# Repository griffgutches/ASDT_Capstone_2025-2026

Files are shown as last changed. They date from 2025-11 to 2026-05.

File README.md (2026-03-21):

# ASDT Datalogger
This PCB is a rocketry flight datalogger with a comprehensive sensor suite.

## Features
- GPS
- Radio
- IMU
- Barometer
- Magnetometer
- Status LEDs
- Reverse polarity protection

## Parts
- ESP32-S3 microcontroller
- u-blox MAX-M10S GPS
- RFM95W-915 radio (SX1276)
- ISM6HG256X High/Low-G IMU
- BMI088 Low-G IMU
- ADXL375 High-G IMU
- MS5607 barometer
- BMP390 barometer
- MMC5983MA magnetometer

## Pinout
| GPIO | Function |
|---|---|
| 0 | BOOT |
| 1 | MS5607 Baro CS |
| 2 | BMP390 Baro CS |
| 4 | MMC598 Mag CS |
| 7 | Radio CS |
| 14 | BMI088 Gyro CS |
| 21 | ADXL375 IMU CS |
| 40 | BMI088 Accel CS |
| 41 | ISM6HG256X IMU CS |
| 11 | ADXL375 INT |
| 13 | Radio INT |
| 18 | BMI088 Accel INT |
| 31 | GPS INT |
| 42 | MMC598 Mag INT |
| 10 | MISO |
| 17 | SCK |
| 44 | MOSI |
| 45 | SCL* |
| 46 | SDA* |
| 25 | Flash I03 |
| 26 | Flash I02 |
| 27 | Flash CS |
| 28 | Flash CLK |
| 29 | Flash IO1 |
| 30 | Flash IO0 |
| 35 | SD CMD |
| 37 | SD data 0 |
| 38 | SD data 1 |
| 33 | SD data 2 |
| 34 | SD data 3 |
| 36 | SD clock |
| 15 | XTAL_32K_P |
| 16 | XTAL_32K_N |
| 19 | USB_D- |
| 20 | USB_D+ |
| 8 | Timepulse |
| 9 | Battery Sense |
| 39 | Buzzer |
| 43 | ANT_SW |
| 6 | Radio Busy |

*SDA/SCL should be moved off GPIO45/46 on future designs because they are strapping pins

## Addresses
| Name | Part | I2C Address |
|---|---|---|
| GPS | MAX-M10S | 0x42 **** |

## Notes
- The boot and reset button on the board are enabled by the jumper J5 on the left side of the board, this jumper must be removed before flight
- The radio **may be damaged** if it is run without an antenna attached
- The LED data pin should never be floating
- The battery sense pin is connected through a 300k-100k voltage divider, so the pin voltage is 0.25 times the battery voltage
- The total current consumption should be below 500mA continuous
- The GPS will blink an LED near the bottom of the board once per second once it gets a fix

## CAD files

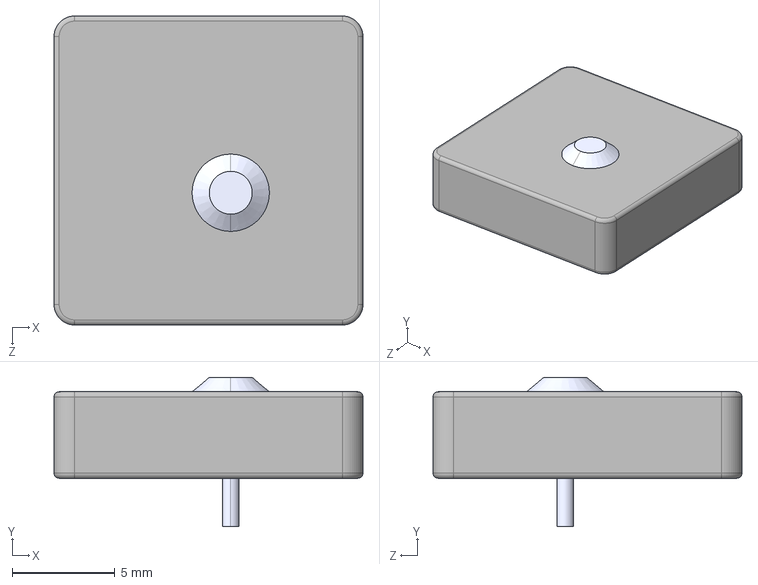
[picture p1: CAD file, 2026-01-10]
Data_Logger_KiCAD/3DModels/YG0043AA.STEP
15.0 x 7.25 x 15.0 mm

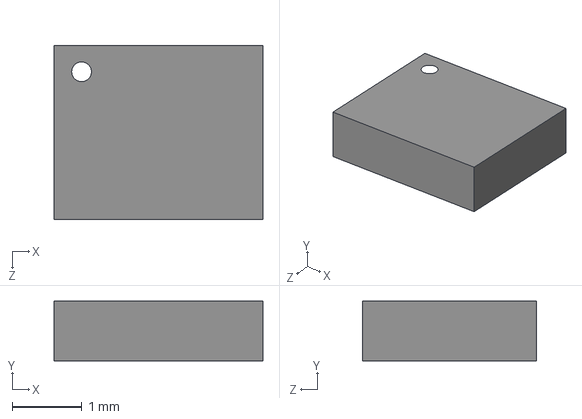
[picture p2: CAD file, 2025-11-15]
Symbol_Files/LSM6DSO32TR/LSM6DSO32TR.step
3.00 x 0.86 x 2.50 mm

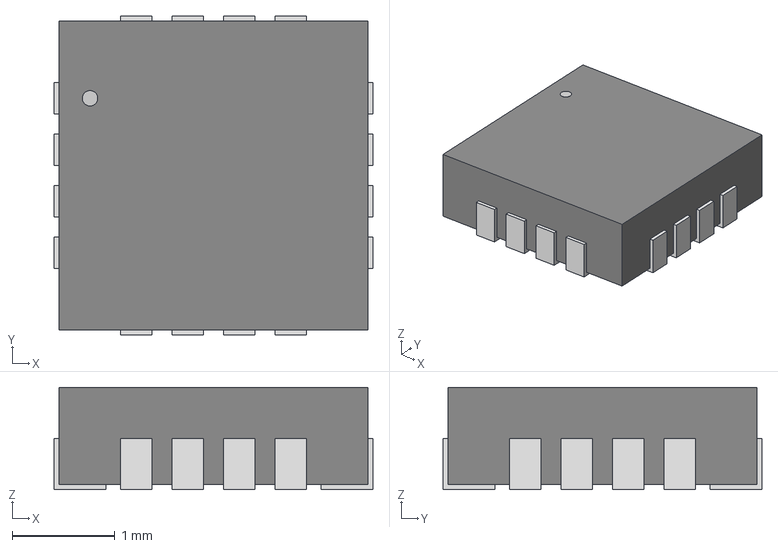
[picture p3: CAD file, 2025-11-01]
Symbol_Files/MMC5983MA_FTP_CAD/MMC5983MA_MEM.step
3.10 x 3.10 x 0.993 mm

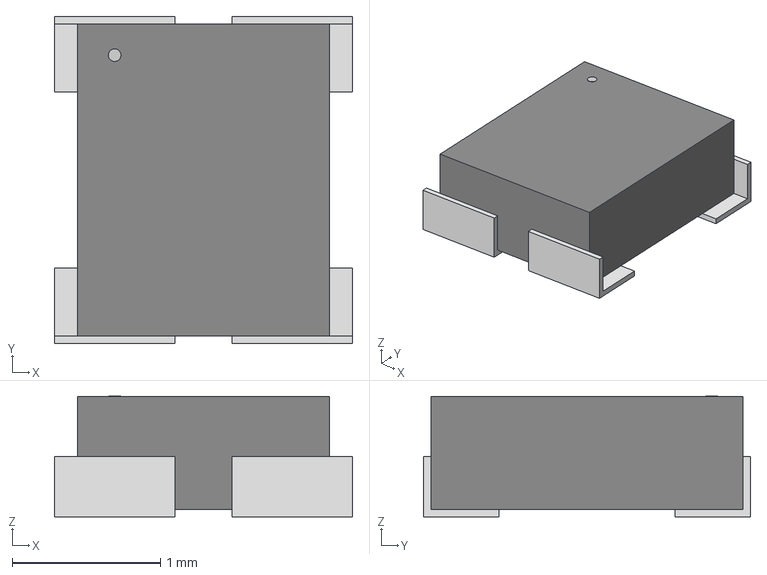
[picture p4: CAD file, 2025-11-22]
Symbol_Files/NT2016SA_32M_END4263A/NT2016SA-32M-END4263A_NDK.step
2.01 x 2.21 x 0.815 mm

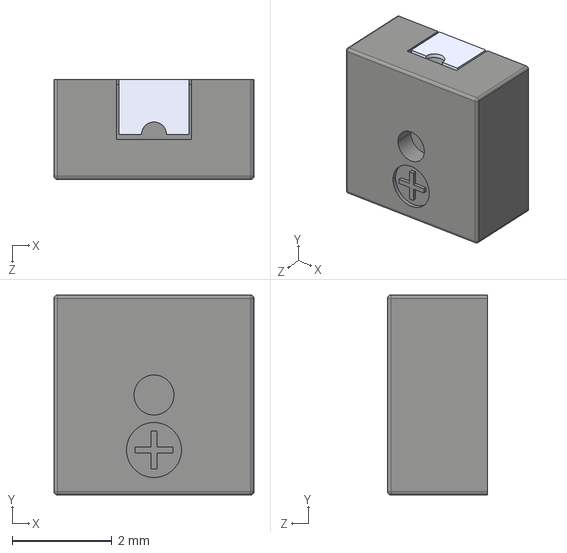
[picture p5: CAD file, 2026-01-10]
Data_Logger_KiCAD/3DModels/Same_Sky_CMT-4023S-SMT-TR.step
4.00 x 4.00 x 2.00 mm

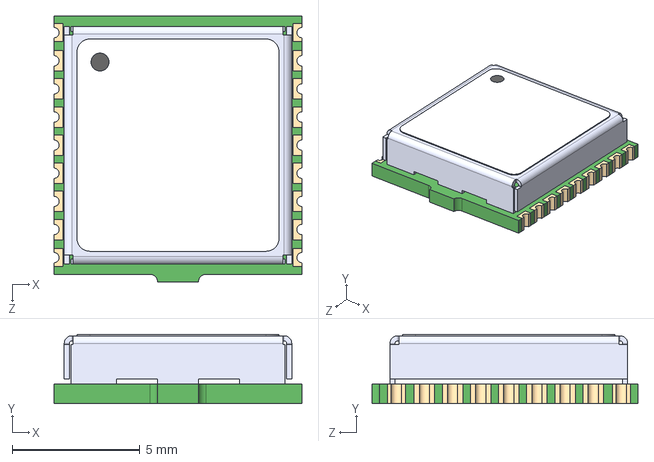
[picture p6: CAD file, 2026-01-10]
Data_Logger_KiCAD/3DModels/MAX-M10S-00B.STEP
9.70 x 2.70 x 10.4 mm

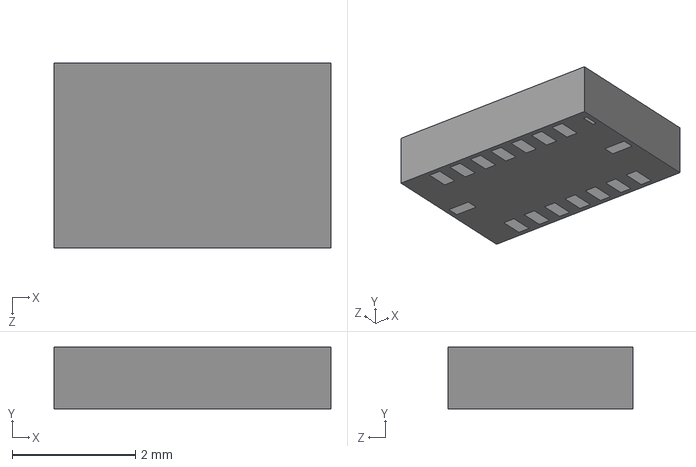
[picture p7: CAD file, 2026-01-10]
Data_Logger_KiCAD/3DModels/BMI088.step
4.50 x 1.00 x 3.00 mm

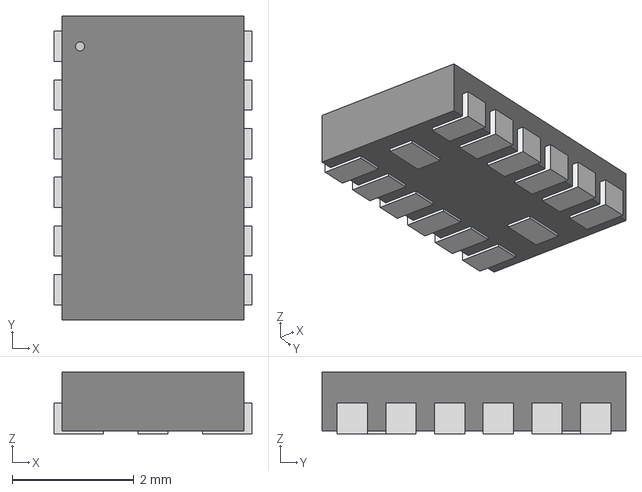
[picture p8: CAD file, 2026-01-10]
Data_Logger_KiCAD/3DModels/adxl375.step
3.25 x 5.00 x 1.02 mm

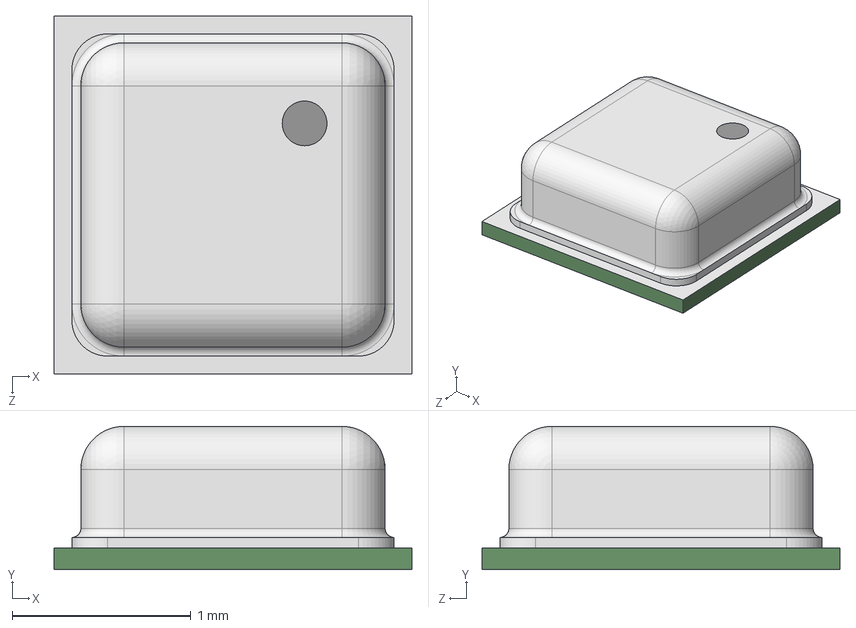
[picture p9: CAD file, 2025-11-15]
Data_Logger_KiCAD/3DModels/BMP390L.step
2.00 x 0.8 x 2.00 mm

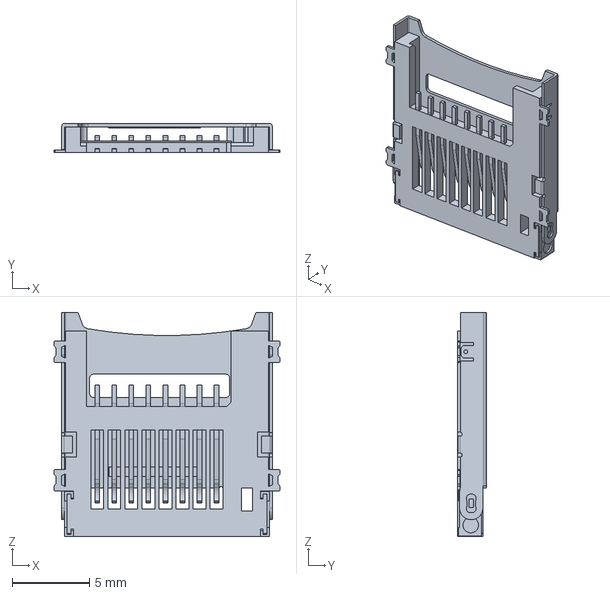
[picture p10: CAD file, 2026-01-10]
Data_Logger_KiCAD/3DModels/472192001.stp
14.6 x 1.90 x 14.5 mm

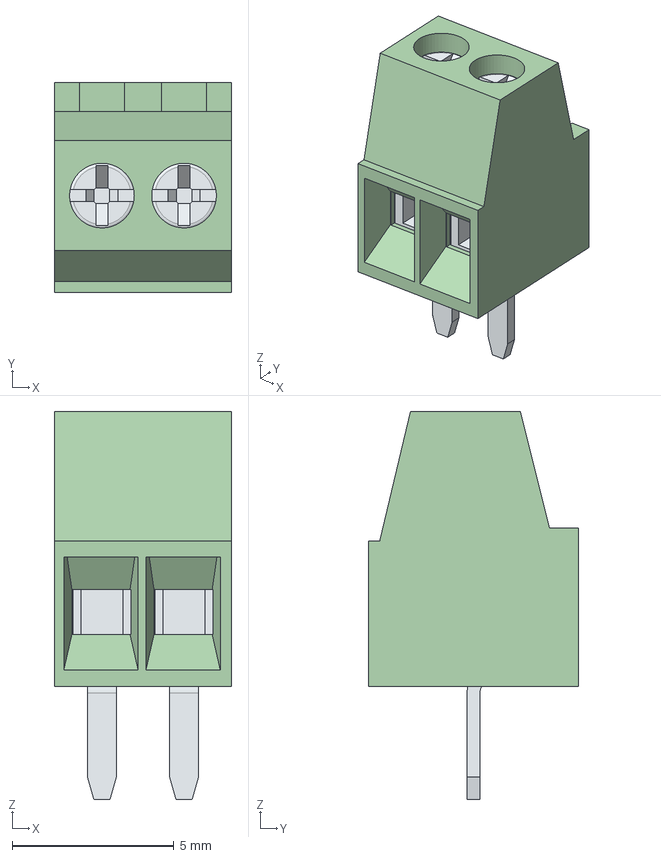
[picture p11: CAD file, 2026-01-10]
Data_Logger_KiCAD/3DModels/691210910002+%28rev1%29.stp
5.48 x 6.50 x 12.0 mm
6912109100xx_CAGE x 2
6912109100xx_PIN x 2
6912109100xx_VIS x 2

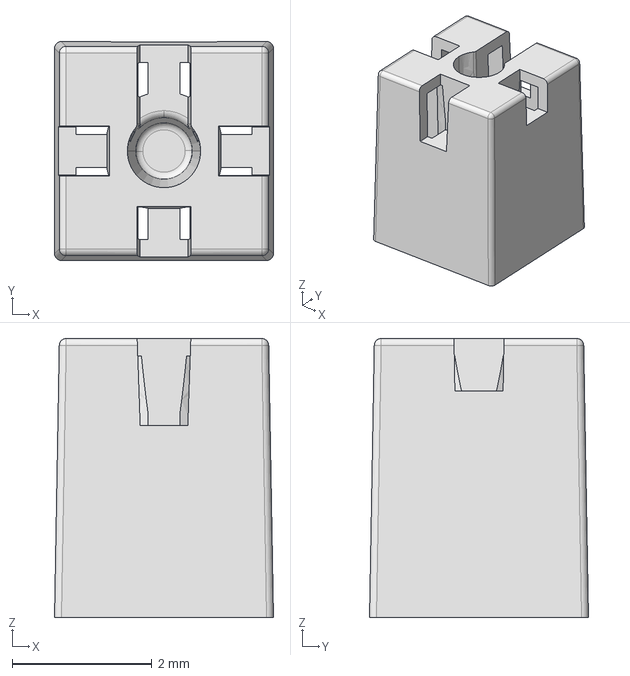
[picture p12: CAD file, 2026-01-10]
Data_Logger_KiCAD/3DModels/0479480001.step
3.14 x 3.14 x 4.00 mm

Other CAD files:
Data_Logger_KiCAD/3DModels/NT2016SA-32M-END4263A_NDK.step

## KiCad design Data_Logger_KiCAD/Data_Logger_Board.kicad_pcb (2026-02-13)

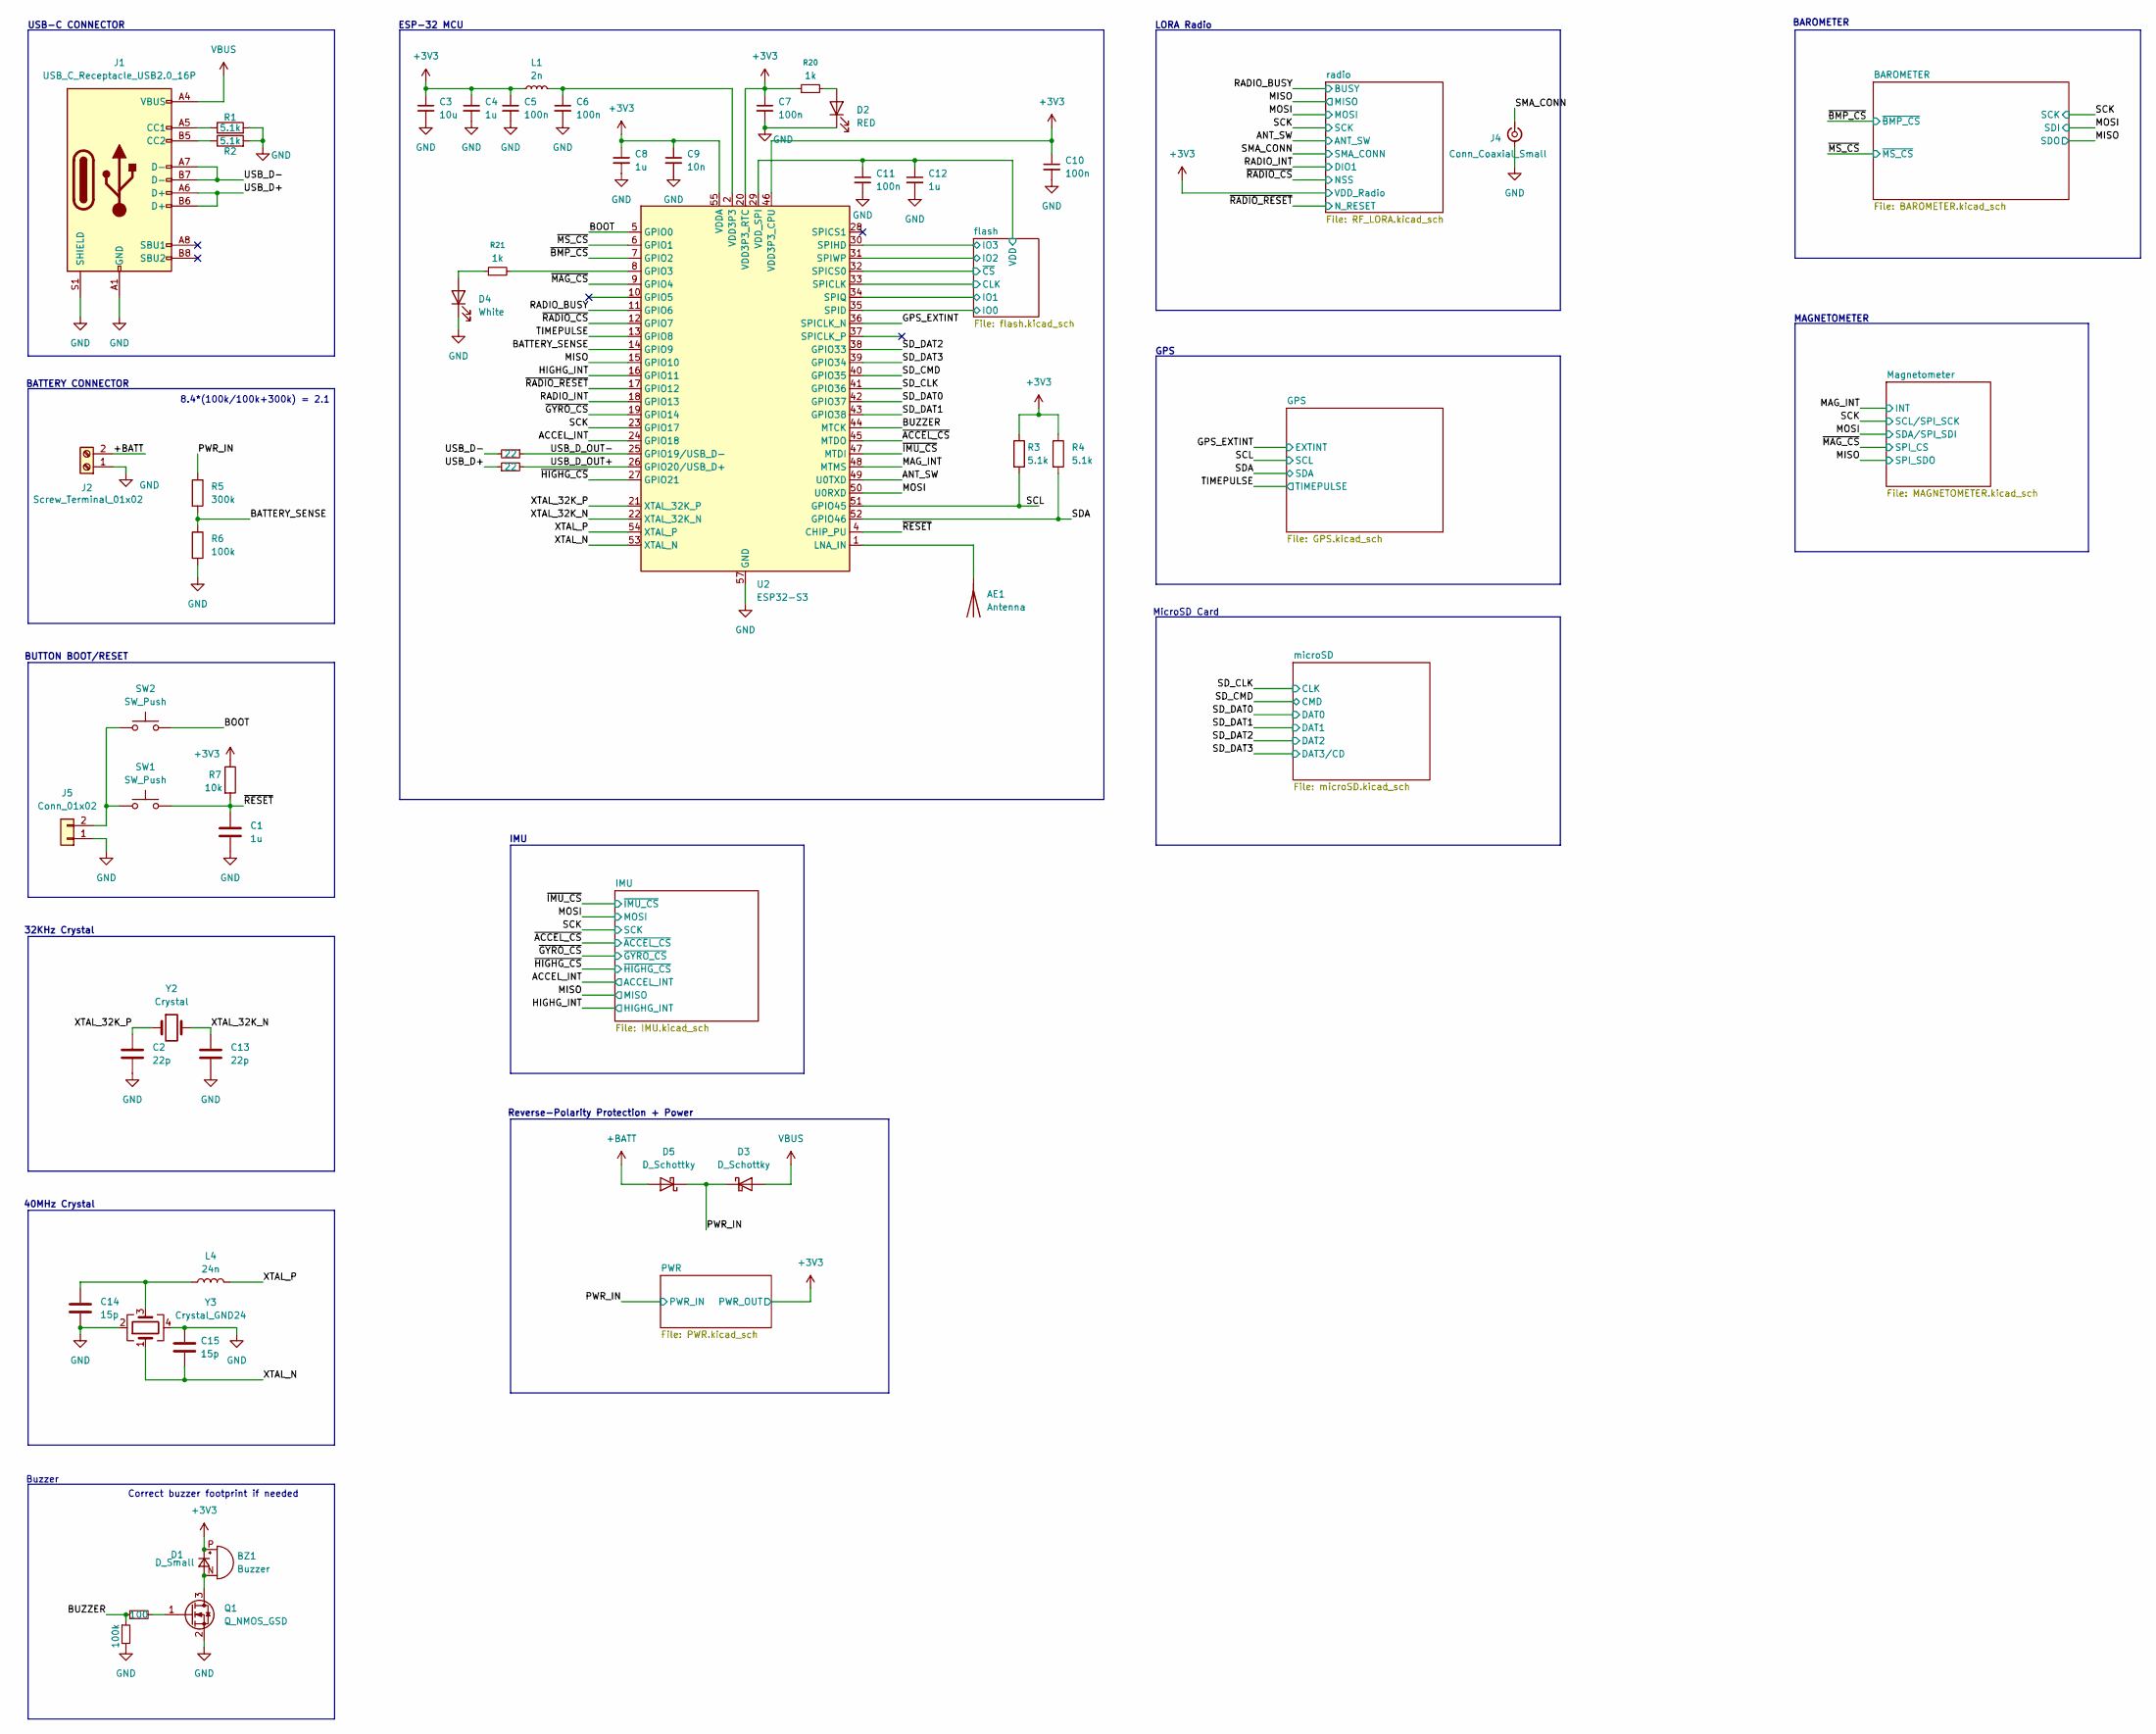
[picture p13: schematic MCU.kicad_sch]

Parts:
AE1: Antenna; Molex_47948-0001_2.4Ghz; LCSC C152351
BZ1: Buzzer; CUI_CMT-4023S-SMT-TR
C1, C4, C8, C12: 1u; C_0402_1005Metric; LCSC C52923
C2, C13: 22p; C_0402_1005Metric; LCSC C1555
C3: 10u; C_0603_1608Metric; LCSC C19702
C5, C6, C7, C10, C11: 100n; C_0402_1005Metric; LCSC C1525
C9: 10n; C_0402_1005Metric; LCSC C15195
C14, C15: 15p; C_0402_1005Metric; LCSC C1548
D1: D_Small; D_SOD-123F; LCSC C64898
D2: RED; LED_0603_1608Metric
D3, D5: D_Schottky; D_SOD-123; LCSC C8598
D4: White; LED_0603_1608Metric
J1: USB_C_Receptacle_USB2.0_16P; USB_C_Receptacle_G-Switch_GT-USB-7010ASV; LCSC C2988369
J2: Screw_Terminal_01x02; TerminalBlock_Xinya_XY308-2.54-2P_1x02_P2.54mm_Horizontal
J4: Conn_Coaxial_Small; SMA_Samtec_SMA-J-P-H-ST-EM1_EdgeMount
J5: Conn_01x02; PinHeader_1x02_P1.27mm_Vertical
L1: 2n; L_0402_1005Metric; LCSC C18216
L4: 24n; L_0402_1005Metric; LCSC C74301
Q1: Q_NMOS_GSD; SOT-23; LCSC C28646273
R1, R2, R3, R4: 5.1k; R_0402_1005Metric; LCSC C25905
R5: 300k; R_0402_1005Metric; LCSC C25774
R6, R14: 100k; R_0402_1005Metric; LCSC C25741
R7: 10k; R_0402_1005Metric; LCSC C25744
R11, R12: 22; R_0402_1005Metric; LCSC C25092
R13: 100; R_0402_1005Metric; LCSC C25076
R20, R21: 1k; R_0402_1005Metric; LCSC C11702
SW1, SW2: SW_Push; SW_SPST_TS-1088-xR020; LCSC C720477
U2: ESP32-S3; QFN-56-1EP_7x7mm_P0.4mm_EP4x4mm; LCSC C2913192
Y2: Crystal; Crystal_SMD_3215-2Pin_3.2x1.5mm; LCSC C32346
Y3: Crystal_GND24; Crystal_SMD_2016-4Pin_2.0x1.6mm; LCSC C501798

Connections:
+3V3: BZ1.P (+), C3.1, C4.1, C5.1, C7.1, C8.1, C9.1, C10.1, D1.1 (K), L1.1, R3.1, R4.1, R7.1, R20.1, U2.20 (VDD3P3_RTC), U2.46 (VDD3P3_CPU), U2.55 (VDDA), U2.56 (VDDA); also elsewhere on the board
+BATT: D5.2 (A), J2.2
/MCU/ACCEL_INT: U2.24 (GPIO18); also elsewhere on the board
/MCU/ANT_SW: U2.49 (U0TXD); also elsewhere on the board
/MCU/BATTERY_SENSE: R5.2, R6.1, U2.14 (GPIO9)
/MCU/BOOT: SW2.2, U2.5 (GPIO0)
/MCU/BUZZER: R13.1, R14.1, U2.44 (MTCK)
/MCU/GPS_EXTINT: U2.36 (SPICLK_N); also elsewhere on the board
/MCU/HIGHG_INT: U2.16 (GPIO11); also elsewhere on the board
/MCU/MAG_INT: U2.48 (MTMS); also elsewhere on the board
/MCU/MISO: U2.15 (GPIO10); also elsewhere on the board
/MCU/MOSI: U2.50 (U0RXD); also elsewhere on the board
/MCU/PWR_IN: D3.1 (K), D5.1 (K), R5.1; also elsewhere on the board
/MCU/RADIO_BUSY: U2.11 (GPIO6); also elsewhere on the board
/MCU/RADIO_INT: U2.18 (GPIO13); also elsewhere on the board
/MCU/SCK: U2.23 (GPIO17); also elsewhere on the board
/MCU/SCL: R3.2, U2.51 (GPIO45); also elsewhere on the board
/MCU/SDA: R4.2, U2.52 (GPIO46); also elsewhere on the board
/MCU/SD_CLK: U2.41 (GPIO36); also elsewhere on the board
/MCU/SD_CMD: U2.40 (GPIO35); also elsewhere on the board
/MCU/SD_DAT0: U2.42 (GPIO37); also elsewhere on the board
/MCU/SD_DAT1: U2.43 (GPIO38); also elsewhere on the board
/MCU/SD_DAT2: U2.38 (GPIO33); also elsewhere on the board
/MCU/SD_DAT3: U2.39 (GPIO34); also elsewhere on the board
/MCU/SMA_CONN: J4.1 (In); also elsewhere on the board
/MCU/TIMEPULSE: U2.13 (GPIO8); also elsewhere on the board
/MCU/USB_D+: J1.A6 (D+), J1.B6 (D+), R12.1
/MCU/USB_D-: J1.A7 (D-), J1.B7 (D-), R11.2
/MCU/USB_D_OUT+: R12.2, U2.26 (GPIO20/USB_D+)
/MCU/USB_D_OUT-: R11.1, U2.25 (GPIO19/USB_D-)
/MCU/XTAL_32K_N: C13.1, U2.22 (XTAL_32K_N), Y2.2
/MCU/XTAL_32K_P: C2.1, U2.21 (XTAL_32K_P), Y2.1
/MCU/XTAL_N: C15.2, U2.53 (XTAL_N), Y3.1
/MCU/XTAL_P: L4.2, U2.54 (XTAL_P)
/MCU/flash/CLK: U2.33 (SPICLK); also elsewhere on the board
/MCU/flash/IO0: U2.35 (SPID); also elsewhere on the board
/MCU/flash/IO1: U2.34 (SPIQ); also elsewhere on the board
/MCU/flash/IO2: U2.31 (SPIWP); also elsewhere on the board
/MCU/flash/IO3: U2.30 (SPIHD); also elsewhere on the board
/MCU/flash/VDD: C11.1, C12.1, U2.29 (VDD_SPI); also elsewhere on the board
/MCU/flash/~CS: U2.32 (SPICS0); also elsewhere on the board
/MCU/~ACCEL_CS: U2.45 (MTDO); also elsewhere on the board
/MCU/~BMP_CS: U2.7 (GPIO2); also elsewhere on the board
/MCU/~GYRO_CS: U2.19 (GPIO14); also elsewhere on the board
/MCU/~HIGHG_CS: U2.27 (GPIO21); also elsewhere on the board
/MCU/~IMU_CS: U2.47 (MTDI); also elsewhere on the board
/MCU/~MAG_CS: U2.9 (GPIO4); also elsewhere on the board
/MCU/~MS_CS: U2.6 (GPIO1); also elsewhere on the board
/MCU/~RADIO_CS: U2.12 (GPIO7); also elsewhere on the board
/MCU/~RADIO_RESET: U2.17 (GPIO12); also elsewhere on the board
/MCU/~RESET: C1.1, R7.2, SW1.2, U2.4 (CHIP_PU)
GND: C1.2, C2.2, C3.2, C4.2, C5.2, C6.2, C7.2, C8.2, C9.2, C10.2, C11.2, C12.2, C13.2, C14.2, C15.1, D2.1 (K), D4.1 (K), J1.A1 (GND), J1.A12 (GND), J1.B1 (GND), J1.B12 (GND), J1.S1 (SHIELD), J2.1, J4.2 (Ext), J5.1, Q1.2 (S), R1.2, R2.2, R6.2, R14.2, U2.57 (GND), Y3.2, Y3.4; also elsewhere on the board
unnamed: AE1.1 (A), U2.1 (LNA_IN)
unnamed: BZ1.N (-), D1.2 (A), Q1.3 (D)
unnamed: C6.1, L1.2, U2.2 (VDD3P3), U2.3 (VDD3P3)
unnamed: C14.1, L4.1, Y3.3
unnamed: D2.2 (A), R20.2
unnamed: D4.2 (A), R21.1
unnamed: J1.A5 (CC1), R1.1
unnamed: J1.B5 (CC2), R2.1
unnamed: J5.2, SW1.1, SW2.1
unnamed: Q1.1 (G), R13.2
unnamed: R21.2, U2.8 (GPIO3)
VBUS: D3.2 (A), J1.A4 (VBUS), J1.A9 (VBUS), J1.B4 (VBUS), J1.B9 (VBUS)

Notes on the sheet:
ESP-32 MCU
Correct buzzer footprint if needed
Buzzer
MAGNETOMETER
Reverse-Polarity Protection + Power
IMU
BATTERY CONNECTOR
BUTTON BOOT/RESET
MicroSD Card
8.4*(100k/100k+300k) = 2.1
32KHz Crystal
40MHz Crystal
BAROMETER
LORA Radio
GPS
USB-C CONNECTOR

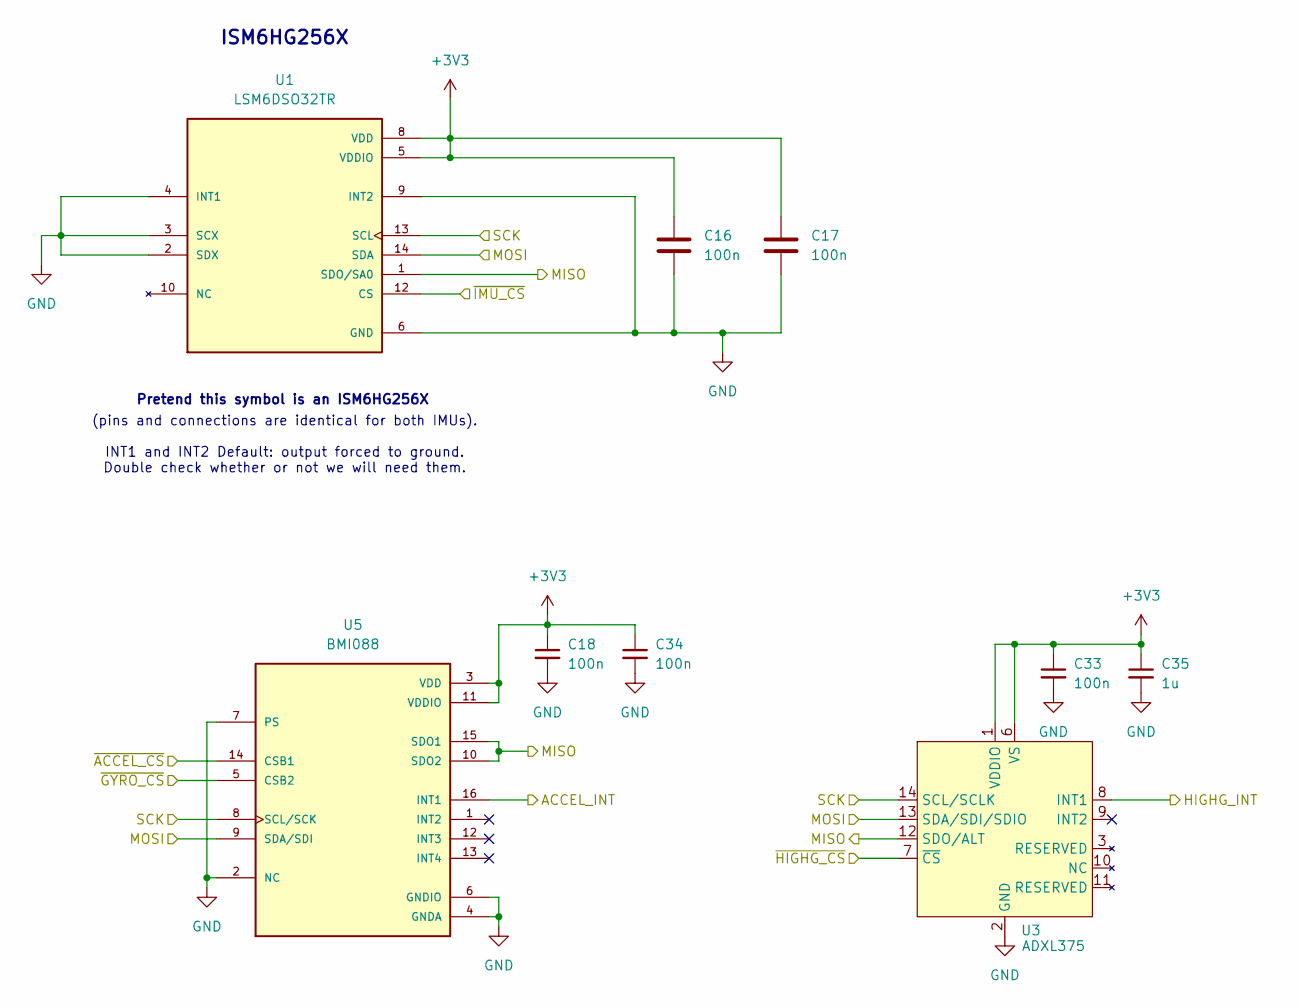
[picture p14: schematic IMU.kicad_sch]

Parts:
C16, C17, C18, C33, C34: 100n; C_0402_1005Metric; LCSC C1525
C35: 1u; C_0402_1005Metric; LCSC C52923
U1: LSM6DSO32TR; LGA-14_3x2.5mm_P0.5mm_LayoutBorder3x4y; PARTREV 1
U3: ADXL375; LGA_CC-14-1_ADI; digikey ADXL375BCCZ-RL7CT-ND
U5: BMI088; PQFN50P450X300X100-16N

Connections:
+3V3: C16.1, C17.1, C18.1, C33.1, C34.1, C35.1, U1.5 (VDDIO), U1.8 (VDD), U3.1 (VDDIO), U3.6 (VS), U5.3 (VDD), U5.11 (VDDIO); also elsewhere on the board
/MCU/ACCEL_INT: U5.16 (INT1); also elsewhere on the board
/MCU/HIGHG_INT: U3.8 (INT1); also elsewhere on the board
/MCU/MISO: U1.1 (SDO/SA0), U3.12 (SDO/ALT), U5.10 (SDO2), U5.15 (SDO1); also elsewhere on the board
/MCU/MOSI: U1.14 (SDA), U3.13 (SDA/SDI/SDIO), U5.9 (SDA/SDI); also elsewhere on the board
/MCU/SCK: U1.13 (SCL), U3.14 (SCL/SCLK), U5.8 (SCL/SCK); also elsewhere on the board
/MCU/~ACCEL_CS: U5.14 (CSB1); also elsewhere on the board
/MCU/~GYRO_CS: U5.5 (CSB2); also elsewhere on the board
/MCU/~HIGHG_CS: U3.7 (~CS); also elsewhere on the board
/MCU/~IMU_CS: U1.12 (CS); also elsewhere on the board
GND: C16.2, C17.2, C18.2, C33.2, C34.2, C35.2, U1.2 (SDX), U1.3 (SCX), U1.4 (INT1), U1.6 (GND), U1.7 (GND), U1.9 (INT2), U3.2 (GND), U3.4 (GND), U3.5 (GND), U5.2 (NC), U5.4 (GNDA), U5.6 (GNDIO), U5.7 (PS); also elsewhere on the board

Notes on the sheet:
Pretend this symbol is an ISM6HG256X
ISM6HG256X
(pins and connections are identical for both IMUs). INT1 and INT2 Default: output forced to ground. Double check whether or not we will need them.

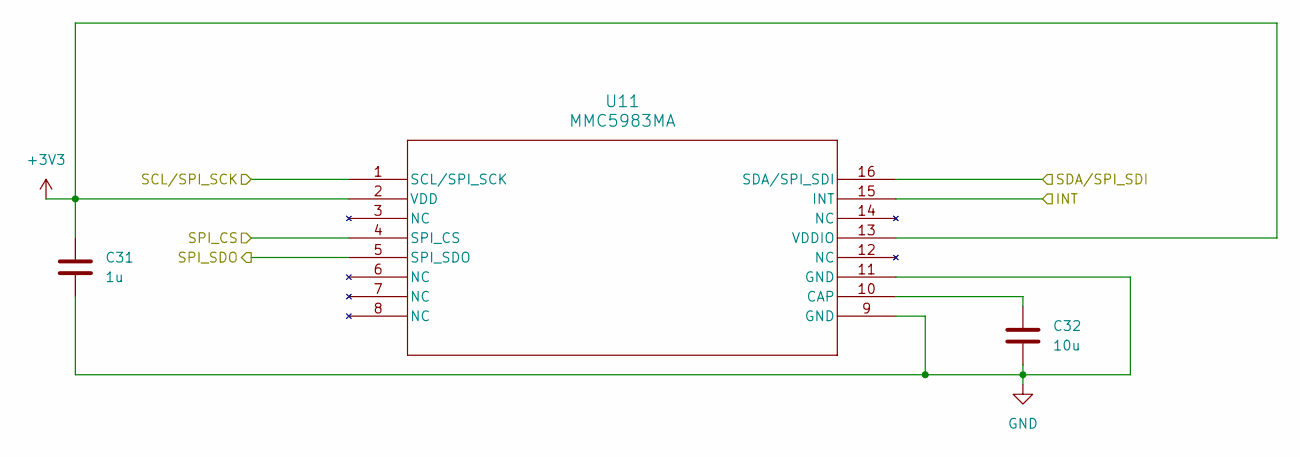
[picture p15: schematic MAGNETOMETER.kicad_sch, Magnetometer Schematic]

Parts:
C31: 1u; C_0402_1005Metric; LCSC C52923
C32: 10u; C_0402_1005Metric; LCSC C15525
U11: MMC5983MA; LGA-16_3x3mm_P0.5mm_LayoutBorder3x5y

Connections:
+3V3: C31.1, U11.2 (VDD), U11.13 (VDDIO); also elsewhere on the board
/MCU/MAG_INT: U11.15 (INT); also elsewhere on the board
/MCU/MISO: U11.5 (SPI_SDO); also elsewhere on the board
/MCU/MOSI: U11.16 (SDA/SPI_SDI); also elsewhere on the board
/MCU/SCK: U11.1 (SCL/SPI_SCK); also elsewhere on the board
/MCU/~MAG_CS: U11.4 (SPI_CS); also elsewhere on the board
GND: C31.2, C32.2, U11.9 (GND), U11.11 (GND); also elsewhere on the board
unnamed: C32.1, U11.10 (CAP)

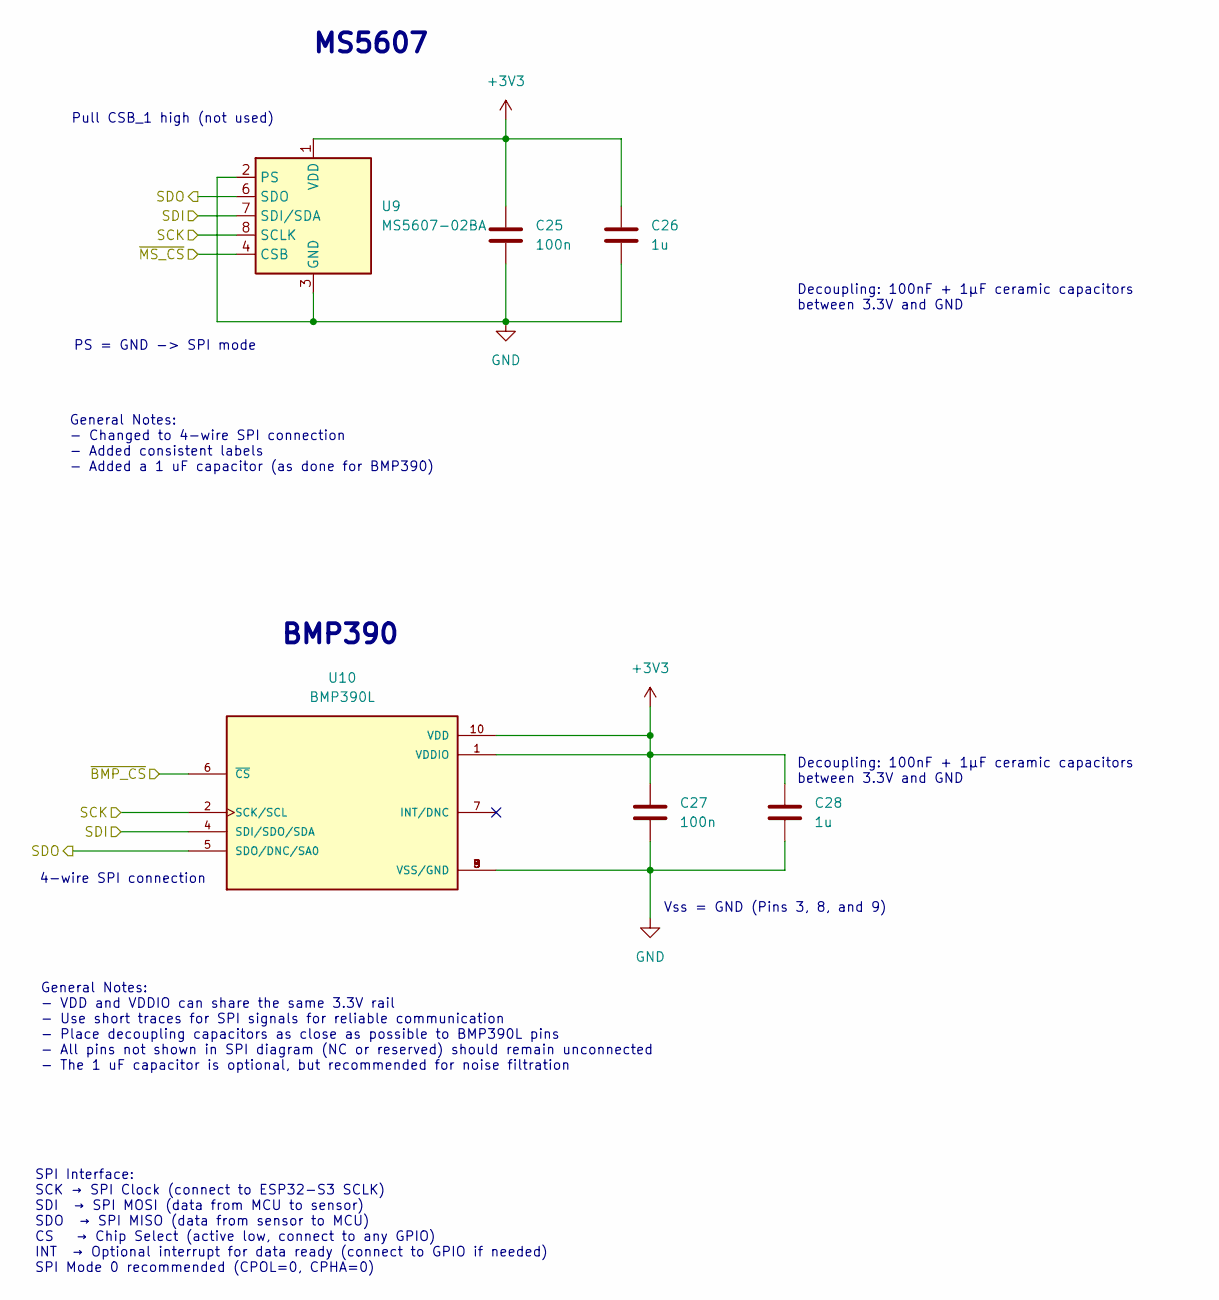
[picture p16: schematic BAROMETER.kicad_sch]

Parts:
C25, C27: 100n; C_0402_1005Metric; LCSC C1525
C26, C28: 1u; C_0402_1005Metric; LCSC C52923
U9: MS5607-02BA; LGA-8_3x5mm_P1.25mm; LCSC C97627
U10: BMP390L; XDCR_BMP390L; PARTREV 1.7

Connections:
+3V3: C25.1, C26.2, C27.1, C28.1, U9.1 (VDD), U10.1 (VDDIO), U10.10 (VDD); also elsewhere on the board
/MCU/MISO: U9.6 (SDO), U10.5 (SDO/DNC/SA0); also elsewhere on the board
/MCU/MOSI: U9.7 (SDI/SDA), U10.4 (SDI/SDO/SDA); also elsewhere on the board
/MCU/SCK: U9.8 (SCLK), U10.2 (SCK/SCL); also elsewhere on the board
/MCU/~BMP_CS: U10.6 (~CS); also elsewhere on the board
/MCU/~MS_CS: U9.4 (CSB), U9.5 (CSB); also elsewhere on the board
GND: C25.2, C26.1, C27.2, C28.2, U9.2 (PS), U9.3 (GND), U10.3 (VSS/GND), U10.8 (VSS/GND), U10.9 (VSS/GND); also elsewhere on the board

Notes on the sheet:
4-wire SPI connection
Decoupling: 100nF + 1µF ceramic capacitors between 3.3V and GND
Vss = GND (Pins 3, 8, and 9)
MS5607
General Notes: - Changed to 4-wire SPI connection - Added consistent labels - Added a 1 uF capacitor (as done for BMP390)
BMP390
PS = GND -> SPI mode
Pull CSB_1 high (not used)
SPI Interface: SCK → SPI Clock (connect to ESP32-S3 SCLK) SDI → SPI MOSI (data from MCU to sensor) SDO → SPI MISO (data from sensor to MCU) CS → Chip Select (active low, connect to any GPIO) INT → Optional interrupt for data ready (connect to GPIO if needed) SPI Mode 0 recommended (CPOL=0, CPHA=0)
General Notes: - VDD and VDDIO can share the same 3.3V rail - Use short traces for SPI signals for reliable communication - Place decoupling capacitors as close as possible to BMP390L pins - All pins not shown in SPI diagram (NC or reserved) should remain unconnected - The 1 uF capacitor is optiona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

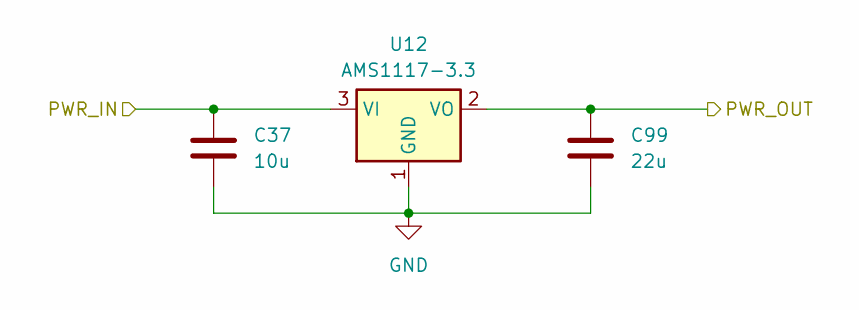
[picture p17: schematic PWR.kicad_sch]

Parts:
C37: 10u; C_0603_1608Metric; LCSC C19702
C99: 22u; C_0603_1608Metric; LCSC C59461
U12: AMS1117-3.3; SOT-223-3_TabPin2; LCSC C6186

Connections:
+3V3: C99.1, U12.2 (VO); also elsewhere on the board
/MCU/PWR_IN: C37.1, U12.3 (VI); also elsewhere on the board
GND: C37.2, C99.2, U12.1 (GND); also elsewhere on the board

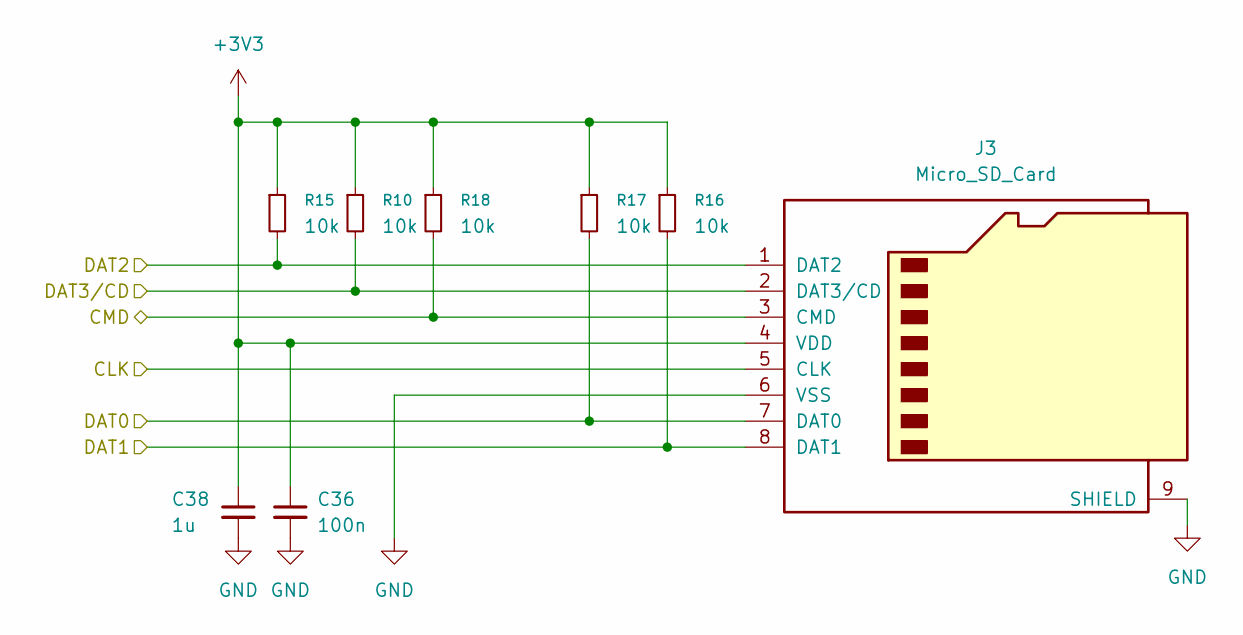
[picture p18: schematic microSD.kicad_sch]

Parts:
C36: 100n; C_0402_1005Metric; LCSC C1525
C38: 1u; C_0402_1005Metric; LCSC C52923
J3: Micro_SD_Card; microSD_HC_Molex_47219-2001; LCSC C164170
R10, R15, R16, R17, R18: 10k; R_0402_1005Metric; LCSC C25744

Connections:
+3V3: C36.1, C38.1, J3.4 (VDD), R10.1, R15.1, R16.1, R17.1, R18.1; also elsewhere on the board
/MCU/SD_CLK: J3.5 (CLK); also elsewhere on the board
/MCU/SD_CMD: J3.3 (CMD), R18.2; also elsewhere on the board
/MCU/SD_DAT0: J3.7 (DAT0), R17.2; also elsewhere on the board
/MCU/SD_DAT1: J3.8 (DAT1), R16.2; also elsewhere on the board
/MCU/SD_DAT2: J3.1 (DAT2), R15.2; also elsewhere on the board
/MCU/SD_DAT3: J3.2 (DAT3/CD), R10.2; also elsewhere on the board
GND: C36.2, C38.2, J3.6 (VSS), J3.9 (SHIELD); also elsewhere on the board

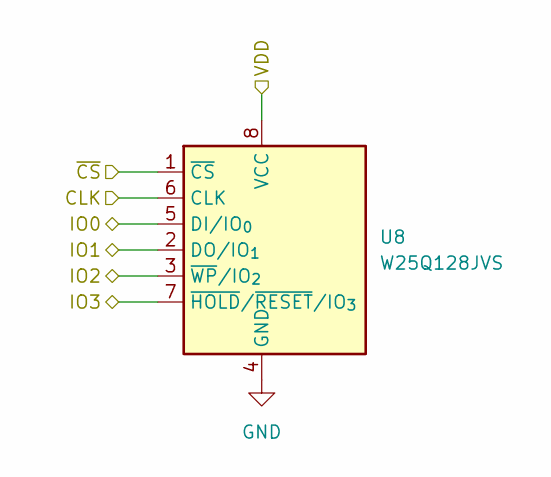
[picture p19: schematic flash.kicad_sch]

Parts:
U8: W25Q128JVS; SOIC-8_5.3x5.3mm_P1.27mm; LCSC C97521

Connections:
/MCU/flash/CLK: U8.6 (CLK); also elsewhere on the board
/MCU/flash/IO0: U8.5 (DI/IO_{0}); also elsewhere on the board
/MCU/flash/IO1: U8.2 (DO/IO_{1}); also elsewhere on the board
/MCU/flash/IO2: U8.3 (~WP/IO_{2}); also elsewhere on the board
/MCU/flash/IO3: U8.7 (~HOLD/~RESET/IO_{3}); also elsewhere on the board
/MCU/flash/VDD: U8.8 (VCC); also elsewhere on the board
/MCU/flash/~CS: U8.1 (~CS); also elsewhere on the board
GND: U8.4 (GND); also elsewhere on the board

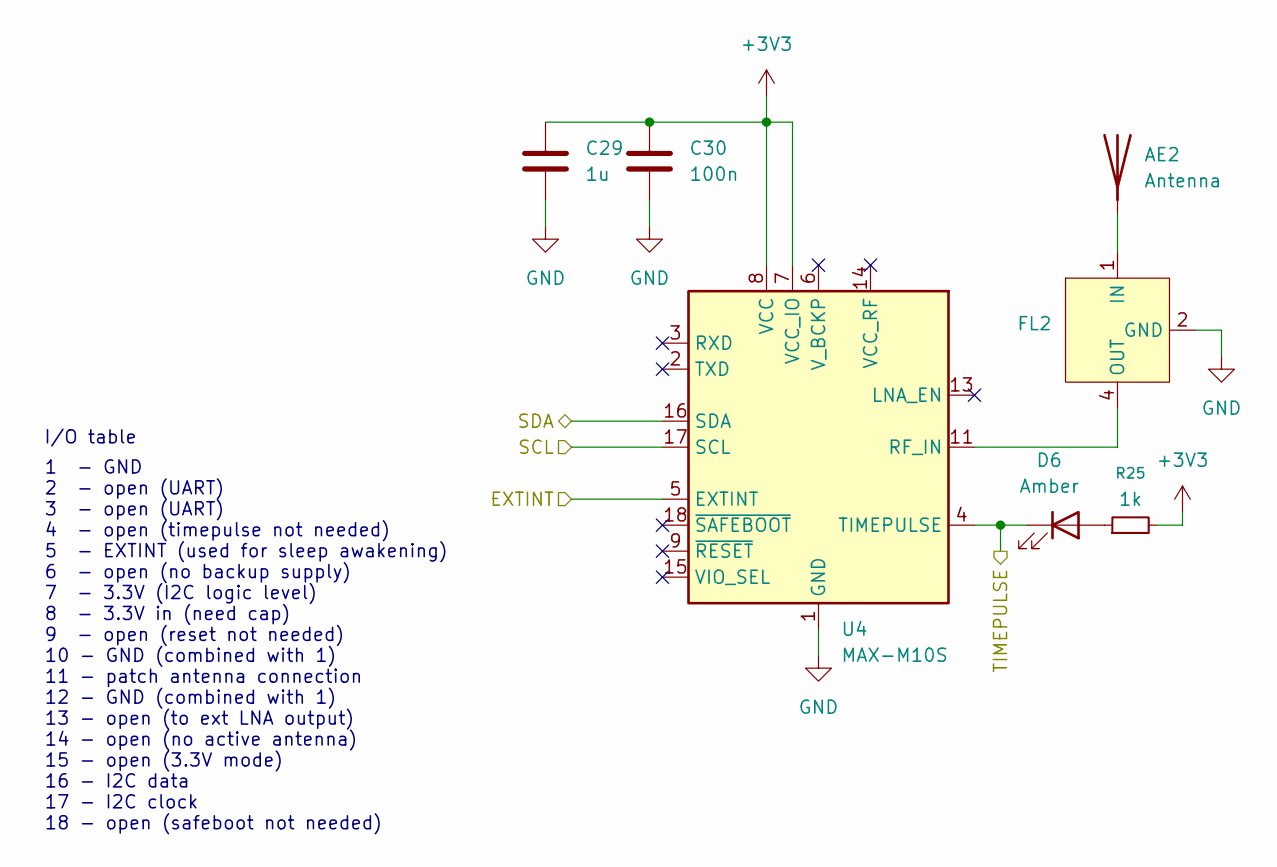
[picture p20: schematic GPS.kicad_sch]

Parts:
AE2: Antenna; YG0043AA
C29: 1u; C_0402_1005Metric; LCSC C52923
C30: 100n; C_0402_1005Metric; LCSC C1525
D6: Amber; LED_0603_1608Metric
FL2: Filter_SAFEA1GXXKA0F00; LCSC C91641
R25: 1k; R_0402_1005Metric; LCSC C11702
U4: MAX-M10S; ublox_MAX

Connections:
+3V3: C29.1, C30.1, R25.2, U4.7 (VCC_IO), U4.8 (VCC); also elsewhere on the board
/MCU/GPS_EXTINT: U4.5 (EXTINT); also elsewhere on the board
/MCU/SCL: U4.17 (SCL); also elsewhere on the board
/MCU/SDA: U4.16 (SDA); also elsewhere on the board
/MCU/TIMEPULSE: D6.1 (K), U4.4 (TIMEPULSE); also elsewhere on the board
GND: C29.2, C30.2, FL2.2 (GND), FL2.3 (GND), FL2.5 (GND), U4.1 (GND), U4.10 (GND), U4.12 (GND); also elsewhere on the board
unnamed: AE2.1 (A), FL2.1 (IN)
unnamed: D6.2 (A), R25.1
unnamed: FL2.4 (OUT), U4.11 (RF_IN)

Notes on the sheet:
1 - GND 2 - open (UART) 3 - open (UART) 4 - open (timepulse not needed) 5 - EXTINT (used for sleep awakening) 6 - open (no backup supply) 7 - 3.3V (I2C logic level) 8 - 3.3V in (need cap) 9 - open (reset not needed) 10 - GND (combined with 1) 11 - patch antenna connection 12 - GND (combined with 1)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
I/O table

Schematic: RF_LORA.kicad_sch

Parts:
C19: 100n; C_0402_1005Metric; LCSC C1525
C20: 1u; C_0402_1005Metric; LCSC C52923
C21: 47n; C_0603_1608Metric; LCSC C1622
C22: 47p; C_0402_1005Metric; LCSC C1567
C23, C24, C41, C42, C43: 1n; C_0402_1005Metric; LCSC C1523
C39: 10n; C_0402_1005Metric; LCSC C15195
C40: 10p; C_0402_1005Metric; LCSC C32949
FB1: FerriteBead_Small; L_0603_1608Metric; LCSC C14709
FL1: 0900FM15K0039; Balun_Johanson_0900FM15K0039
L2, L3: 47n; L_0402_1005Metric; LCSC C27151
R8, R9: 100; R_0402_1005Metric; LCSC C25076
R19: 220; R_0402_1005Metric; LCSC C25091
U6: SX1262IMLTRT; QFN-24-1EP_4x4mm_P0.5mm_EP2.6x2.6mm
U7: MASW-007221; SOT-363_SC-70-6
XTAL3: NT2016SA-32M-END4263A; NT2016SA-32M-END4263A_NDK; LCSC C36338880

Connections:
+3V3: FB1.2; also elsewhere on the board
/MCU/ANT_SW: R9.1; also elsewhere on the board
/MCU/MISO: U6.16 (MISO); also elsewhere on the board
/MCU/MOSI: U6.17 (MOSI); also elsewhere on the board
/MCU/RADIO_BUSY: U6.14 (BUSY); also elsewhere on the board
/MCU/RADIO_INT: U6.13 (DIO1); also elsewhere on the board
/MCU/SCK: U6.18 (SCK); also elsewhere on the board
/MCU/SMA_CONN: C41.2; also elsewhere on the board
/MCU/radio/DIO2: R8.1, U6.12 (DIO2)
/MCU/radio/TCXO_VCC: C39.1, U6.6 (DIO3), XTAL3.4 (VCC)
/MCU/radio/XTA: R19.2, U6.3 (XTA)
/MCU/~RADIO_CS: U6.19 (NSS); also elsewhere on the board
/MCU/~RADIO_RESET: U6.15 (~RESET); also elsewhere on the board
GND: C19.2, C20.1, C21.2, C22.2, C23.2, C24.2, C39.2, FL1.2 (GND), FL1.5 (GND), FL1.7 (GND), FL1.9 (GND), FL1.10 (GND), U6.2 (GND), U6.5 (GND), U6.8 (GND), U6.20 (GND), U6.25 (GND), U7.2 (GND), XTAL3.1 (GND), XTAL3.2 (GND); also elsewhere on the board
unnamed: C40.2, R19.1
unnamed: FL1.3 (RFI_N), U6.22 (RFI_N)
unnamed: FL1.4 (RFI_P), U6.21 (RFI_P)
unnamed: FL1.1 (RFO), L3.2, U6.23 (RFO)
unnamed: C42.1, FL1.6 (SW_RFI)
unnamed: C43.1, FL1.8 (SW_RFO)
unnamed: L2.1, U6.9 (DCC_SW)
unnamed: C19.1, FB1.1, U6.1 (VDD_IN), U6.10 (VBAT), U6.11 (VBAT_IO)
unnamed: C20.2, L2.2, U6.7 (VREG)
unnamed: C21.1, C22.1, L3.1, U6.24 (VR_PA)
unnamed: C43.2, U7.1 (RF1)
unnamed: C42.2, U7.3 (RF2)
unnamed: C41.1, U7.5 (RFC)
unnamed: C23.1, R8.2, U7.6 (V1)
unnamed: C24.1, R9.2, U7.4 (V2)
unnamed: C40.1, XTAL3.3 (OUT)

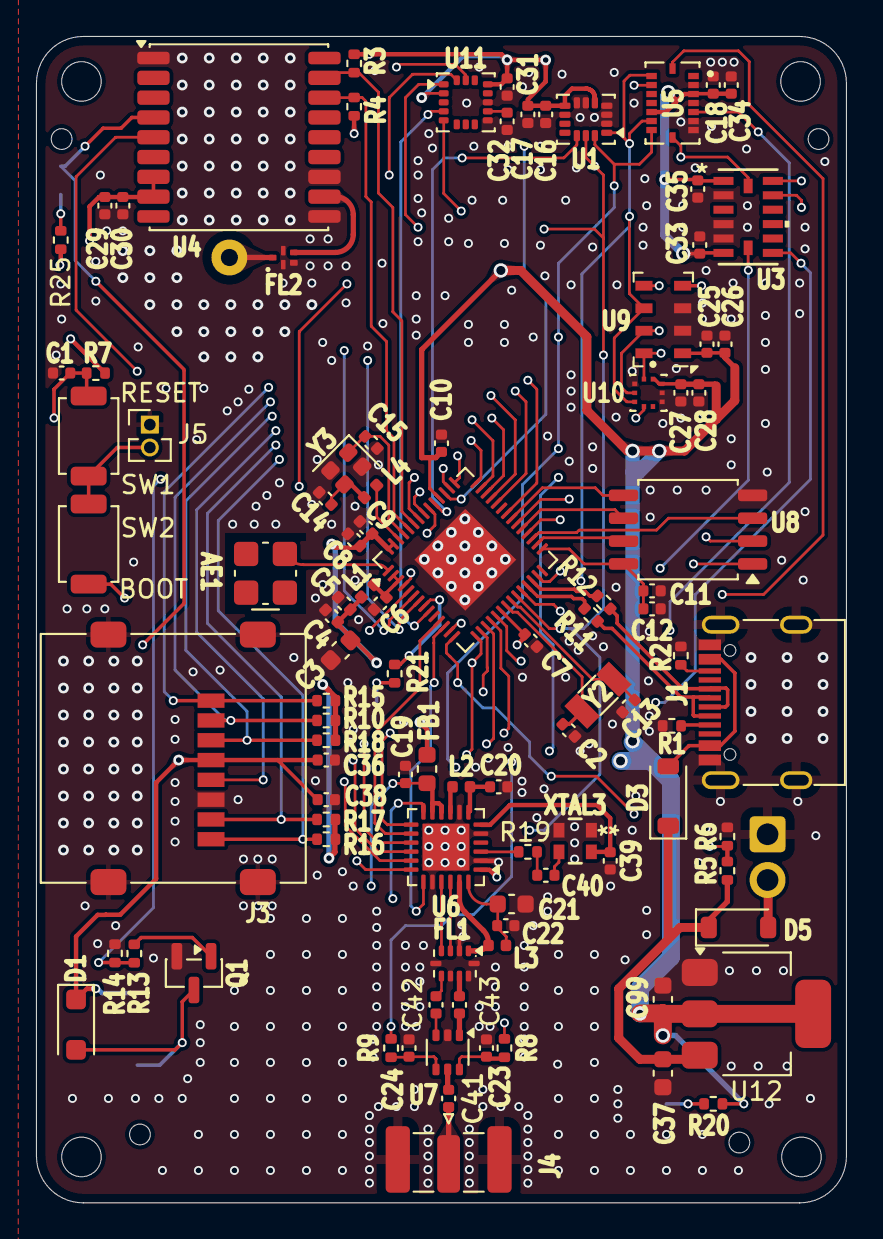
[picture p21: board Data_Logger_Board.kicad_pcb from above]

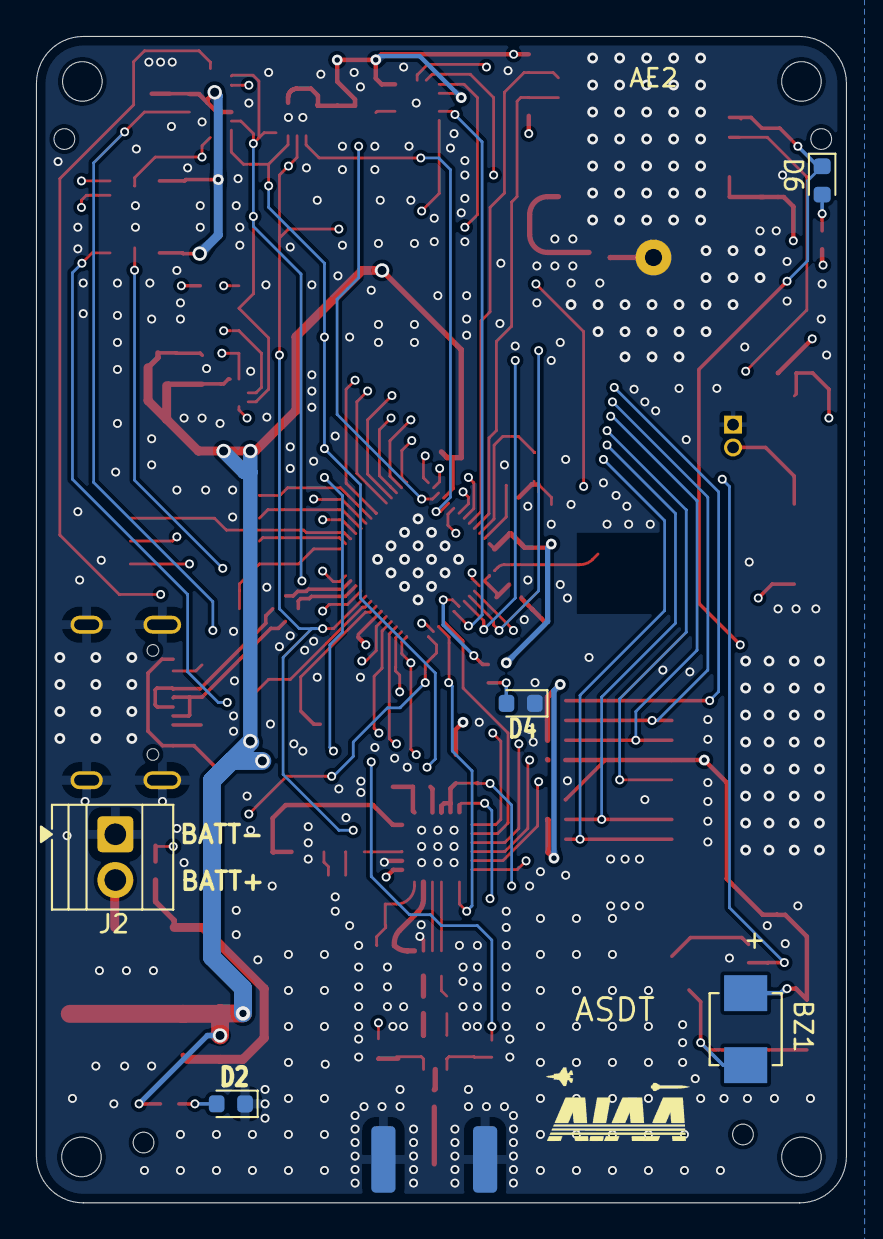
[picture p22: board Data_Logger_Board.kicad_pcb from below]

Board: 4 copper layers, 45.0 x 64.8 mm, 109 parts (6 on the bottom side), 87 nets.

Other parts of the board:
H1, H2, H3, H4: MountingHole; MountingHole_2.2mm_M2

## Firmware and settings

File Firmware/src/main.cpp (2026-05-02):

//#include <Arduino.h>
#include <pins.h>
#include <SPI.h>
#include <MS5611_SPI.h>
#include <ISM6HG256XSensor.h>
//#include <SparkFun_u-blox_GNSS_v3.h>
#include "led.h"
#include "ina745.h"
#include "microsd.h"

SPIClass mySPI(HSPI);

MS5611_SPI baro(MS5607_CS, &mySPI);

// ISM6HG256XSensor imu(&mySPI, ISM6HG256X_IMU_CS);

//SFE_UBLOX_GNSS myGNSS;
void Sensorscode(void * parameter);
void Storingcode(void * parameter);

TaskHandle_t Sensors;
TaskHandle_t Storing;

LogEntry buffer1[16384 / sizeof(LogEntry)];
LogEntry buffer2[16384 / sizeof(LogEntry)];
LogEntry* currentBuffer = buffer1;
int entryCount = 0;
volatile bool bufferReady = false;
LogEntry* bufferToSave = nullptr;
//static ulong last_measurement = 2217;

void setup() {

  mySPI.begin(SPI_SCK, SPI_MISO, SPI_MOSI);
  pinMode(MS5607_CS, OUTPUT);
  pinMode(BMP390_CS, OUTPUT);
  pinMode(ISM6HG256X_IMU_CS, OUTPUT);
  pinMode(BMI088_ACCEL_CS, OUTPUT);
  pinMode(BMI088_GYRO_CS, OUTPUT);
  pinMode(ADXL375_IMU_CS, OUTPUT);
  pinMode(RADIO_CS, OUTPUT);
  pinMode(MAG_CS, OUTPUT);

  pinMode(BATTERY_SENSE, INPUT);

  digitalWrite(MS5607_CS, HIGH);
  digitalWrite(BMP390_CS, HIGH);
  digitalWrite(ISM6HG256X_IMU_CS, HIGH);
  digitalWrite(BMI088_ACCEL_CS, HIGH);
  digitalWrite(BMI088_GYRO_CS, HIGH);
  digitalWrite(ADXL375_IMU_CS, HIGH);
  digitalWrite(RADIO_CS, HIGH);
  digitalWrite(MAG_CS, HIGH);
  
  baro.setSPIspeed(10000000);



  Serial.begin(9600);
  delay(2000);         // delay(2000);   // Replace sleep_ms()for ESP32
  Serial.println("test");



  Serial.println("baro.begin()");
  if (baro.begin() == true) {
    Serial.print("MS5611 found: ");
    Serial.println(baro.getDeviceID(), HEX);
  } else {
    while (true) {
      Serial.println("MS5611 not found. halt.");
      delay(1);
    }
  }
  baro.reset(1);

  // int imu_status = imu.begin();
  // if (imu_status != 0) {
  //   Serial.println("IMU error");
  // }
  // Serial.println("IMU detected");
  // imu.Enable_X();
  // imu.Enable_G();

  // imu.Set_X_FullScale(8);

  Wire.begin(4, 5);      // SDA, SCL
  Wire.setClock(100000); // => 100kHz I2C clock speed


  // Initialize SD here on Core 1
  SD_MMC.setPins(SD_CLOCK, SD_CMD, SD_DATA_0, SD_DATA_1, SD_DATA_2, SD_DATA_3);

  //true for 1-bit, false for 4-bit
  if (!SD_MMC.begin("/sdcard", false)) {
    Serial.println("SD_MMC mount failed");
    return;
  }
  Serial.println("SD_MMC mounted");

  //
  // if (myGNSS.begin() == false) {
  //   Serial.println(F("u-blox GNSS not detected. Check wiring/address."));
  //   while (1);
  // }
  //
  xTaskCreatePinnedToCore(
                    Sensorscode,   /* Task function. */
                    "Sensors",     /* name of task. */
                    10000,       /* Stack size of task */
                    NULL,        /* parameter of the task */
                    1,           /* priority of the task */
                    &Sensors,      /* Task handle to keep track of created task */
                    1);          /* pin task to core 0 */                  
  delay(500); 
  xTaskCreatePinnedToCore(
                    Storingcode,   /* Task function. */
                    "Storing",     /* name of task. */
                    10000,       /* Stack size of task */
                    NULL,        /* parameter of the task */
                    1,           /* priority of the task */
                    &Storing,      /* Task handle to keep track of created task */
                    0);          /* pin task to core 1 */                  

  
}

void loop() {

}

void Sensorscode(void * parameter) {
  while (true) {
    static ulong last_measurement_us = 0;
    if (micros() - last_measurement_us >= 10000) {
      last_measurement_us = micros();
      int e = baro.read();
      if (e != MS5611_READ_OK) {
        Serial.print("barometer error = ");
        Serial.println(e);
      }
      //currentBuffer[entryCount].ms = last_measurement;
      currentBuffer[entryCount].temp = baro.getTemperature();
      currentBuffer[entryCount].press = baro.getPressure();

      //Serial.println(baro.getTemperature(), 2);
      //Serial.println(baro.getPressure(), 2);
      
      //ISM6HG256X_Axes_t accel, rot_rate;
      //imu.Get_X_Axes(&accel);
      //imu.Get_G_Axes(&rot_rate);
      //currentBuffer[entryCount].accX = accel.x;
      //currentBuffer[entryCount].accY = accel.y;
      //currentBuffer[entryCount].accZ = accel.z;
      //currentBuffer[entryCount].gyroX = rot_rate.x;
      //currentBuffer[entryCount].gyroY = rot_rate.y;
      //currentBuffer[entryCount].gyroZ = rot_rate.z;
      currentBuffer[entryCount].test = 0xFF;
      
      //last_measurement ++;
  

      entryCount++;
      if (entryCount >= (16384 / sizeof(LogEntry))) {
        bufferToSave = currentBuffer;
        bufferReady = true;

        // Switch to the other bucket
        currentBuffer = (currentBuffer == buffer1) ? buffer2 : buffer1;
        
        entryCount = 0;
      }
    }
    vTaskDelay(1);
  }
}

void Storingcode(void * parameter) {
  while (true) {
    if (bufferReady) {
      File f = SD_MMC.open("/data500.bin", FILE_APPEND);
      if (f) {
        f.write((uint8_t*)bufferToSave, 16384);
        f.close();
        Serial.println("Written to file");
      }
      bufferReady = false; // Reset the flag
    }
    vTaskDelay(1);
  }
}


//   static ulong last_measurement_us = 0;
  
//   //if (millis() - last_measurement >= 1) {
//   if (micros() - last_measurement_us >= 10000) {
//     last_measurement_us = micros();
//     int e = baro.read();
//     if (e != MS5611_READ_OK) {
//       Serial.print("barometer error = ");
//       Serial.println(e);
//     }
//     //test_sd_speed();
//     currentBuffer[entryCount].ms = last_measurement;
//     currentBuffer[entryCount].temp = baro.getTemperature();
//     currentBuffer[entryCount].press = baro.getPressure();
//     // Serial.print("Barometer\n");
//     // Serial.print("T:\t");
//     // Serial.print(baro.getTemperature(), 2);
//     // Serial.print("\tP:\t");
//     // Serial.print(baro.getPressure(), 2);
//     // Serial.println();
//     // Serial.println();

//     //float battery_voltage = ((float)analogRead(BATTERY_SENSE)) / (0.3311 * 4096.0);
//     //Serial.printf("Battery voltage = %fV\n", battery_voltage);

//     // Add following two lines for ESP32:
//     // analogReadResolution(12);
//     // analogSetAttenuation(ADC_11db);

//     ISM6HG256X_Axes_t accel, rot_rate;
//     imu.Get_X_Axes(&accel);
//     imu.Get_G_Axes(&rot_rate);
//     currentBuffer[entryCount].accX = accel.x;
//     currentBuffer[entryCount].accY = accel.y;
//     currentBuffer[entryCount].accZ = accel.z;
//     currentBuffer[entryCount].gyroX = rot_rate.x;
//     currentBuffer[entryCount].gyroY = rot_rate.y;
//     currentBuffer[entryCount].gyroZ = rot_rate.z;
//     // Serial.println("IMU:");
//     // Serial.printf("Acceleration %d %d %d\n", accel.x, accel.y, accel.z);
//     // Serial.printf("Rotation Rate %d %d %d\n\n", rot_rate.x, rot_rate.y, rot_rate.z);

    
    
//     // currentBuffer[entryCount].magX = event.magnetic.x;
//     // currentBuffer[entryCount].magY = event.magnetic.y;
//     // currentBuffer[entryCount].magZ = event.magnetic.z;
//     currentBuffer[entryCount].test = 0xFF;
//     //Serial.printf("Magnetometer:\n %f %f %f\n\n", event.magnetic.x, event.magnetic.y, event.magnetic.z);

//     // if (myGNSS.getPVT()) {
//     // long latitude = myGNSS.getLatitude(); // Degrees * 10^-7
//     // long longitude = myGNSS.getLongitude();
//     // long altitude = myGNSS.getAltitude(); // mm above ellipsoid
//     // byte SIV = myGNSS.getSIV();           // Satellites in View
//     // }
//     last_measurement ++;
    

//     entryCount++;
//     if (entryCount >= (16384 / sizeof(LogEntry))) {
//       bufferToSave = currentBuffer;
//       bufferReady = true;

//       // Switch to the other bucket
//       currentBuffer = (currentBuffer == buffer1) ? buffer2 : buffer1;
      
//       entryCount = 0;
//     }
//   }
// }

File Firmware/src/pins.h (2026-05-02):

#pragma once


#define MS5607_CS              1
#define BMP390_CS              2
#define MAG_CS                 4
#define RADIO_CS               7
#define BMI088_GYRO_CS         14
#define ADXL375_IMU_CS         21
#define BMI088_ACCEL_CS        40
#define ISM6HG256X_IMU_CS      41

#define ADXL375_INT            11
#define RADIO_INT              13
#define BMI088_ACCEL_INT       18
#define GPS_INT                31
#define MMC598_MAG_INT         42

#define SPI_MISO               10
#define SPI_SCK                17
#define SPI_MOSI               44
#define I2C_SCL                45
#define I2C_SDA                46

#define FLASH_I03              25
#define FLASH_I02              26
#define FLASH_CS               27
#define FLASH_CLK              28
#define FLASH_IO1              29
#define FLASH_IO0              30

#define SD_CMD                 35
#define SD_DATA_0              37
#define SD_DATA_1              38
#define SD_DATA_2              33
#define SD_DATA_3              34
#define SD_CLOCK               36

#define TIMEPULSE              8
#define BATTERY_SENSE          9
#define BUZZER                 39
#define ANT_SW                 43
#define RADIO_BUSY             6

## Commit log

2025-11-01 Commit Initial Schematic Files
    [BAROMETER.kicad_sch, Data_Logger_Board.kicad_pcb, Data_Logger_Board.kicad_sch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]
2025-11-01 add gps schem
    [GPS_sensor.kicad_sch]
2025-11-01 Imported Barometer Into Main Branch
    [BAROMETER.kicad_sch, Barometers_ASDT_Capstone.kicad_sch]
2025-11-01 add whole project file
    [GPS_sensor.kicad_pcb, GPS_sensor.kicad_sch]
2025-11-01 Sub-schematics Generated
    [BAROMETER.kicad_sch, Data_Logger_Board.kicad_sch, MAGNETOMETER.kicad_sch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]
2025-11-01 add gps sensor
    [GPS_sensor.kicad_sch]
2025-11-01 Radio Layout V1.0
    [BAROMETER.kicad_sch, Data_Logger_Board.kicad_pcb, Data_Logger_Board.kicad_sch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]
2025-11-01 esp32 schem add
    [GPS_sensor.kicad_sch, esp32.kicad_pcb, esp32.kicad_sch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]
2025-11-07 esp32 edits
    [esp32.kicad_sch]
2025-11-08 minor updates
    [Data_Logger_Board.kicad_sch, GPS.kicad_sch, MCU.kicad_sch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]
2025-11-08 Aggregated sub schematics into single primary schematic
    [BAROMETER.kicad_sch, Data_Logger_Board.kicad_sch, GPS.kicad_sch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]
2025-11-09 add I/O to GPS sheet
    [MCU.kicad_sch]
2025-11-09 remove old esp/gps files
    [GPS_sensor.kicad_pcb, GPS_sensor.kicad_sch, esp32.kicad_pcb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]
2025-11-15 add more I/O to MCU
    [MCU.kicad_sch]
2025-11-15 Organization and LSM6DSO32 (IMU) schematic
    [BMP390L.step, Barometers_ASDT_Capstone.kicad_pcb, Barometers_ASDT_Capstone.kicad_sch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]
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2025-11-15 Added first IMU schematic.
    [IMUs.kicad_pcb, IMUs.kicad_sch]
2025-11-15 Added second IMU schematic.
    [IMUs.kicad_sch]
2025-11-15 Simplified Naming Convention
    [Barometers.kicad_pcb, Barometers.kicad_sch, IMUs.kicad_pcb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]
2025-11-15 update changes to MCU, add gitignore
    [GPS.kicad_sch, MAGNETOMETER.kicad_sch, MCU.kicad_sch]
2025-11-16 add footprint/LCSC to parts
    [BAROMETER.kicad_sch, GPS.kicad_sch, IMU.kicad_sch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]
2025-11-16 make DIO2 local
    [RF_LORA.kicad_sch]
2025-11-16 update sheet pins
    [MCU.kicad_sch]
2025-11-16 add more footprints
    [MCU.kicad_sch]
2025-11-21 added footprints to barometer project
    [Barometers.kicad_pcb, Barometers.kicad_sch]
2025-11-21 Barometer layout draft created
    [Barometers.kicad_pcb]
2025-11-22 adding labels and updating IMU sch
    [GPS.kicad_sch, IMU.kicad_sch, MCU.kicad_sch]
2025-11-22 update MCU
    [MCU.kicad_sch]
2025-11-22 add CS's
    [IMU.kicad_sch, MCU.kicad_sch]
2025-11-22 Added NT2016 TCXO Symbol and Footprint
    Added NT2016 TCXO Symbol and Footprint
    [NT2016SA-32M-END4263A_NDK.step, RF_LORA.kicad_sch]
2025-11-22 Magnetometer Footprint Added
    Magnetometer Footprint Added
    [MAGNETOMETER.kicad_sch, RF_LORA.kicad_sch]
2025-11-22 synced sheet pins in Data_Logger_Board_pro
    [BAROMETER.kicad_sch, GPS.kicad_sch, MAGNETOMETER.kicad_sch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]
2025-11-22 added pwr schematic.
    [PWR.kicad_sch]
2025-11-22 update IO
    [PWR.kicad_sch]
2025-11-22 Updated pwr labels and sheet pins
    [MCU.kicad_sch]
2025-11-23 Revert "Updated pwr labels and sheet pins"
    This reverts commit 1a9ac38adf7d5b931f8e0b911fe1764f57823125.
    [MCU.kicad_sch]
2025-11-23 diode part#
    [MCU.kicad_sch]
2025-11-29 rem old files and add LCSC #'s
    [BAROMETER.kicad_sch, Barometers.kicad_pcb, Barometers.kicad_sch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]
2025-12-04 update pcb and create .bkp backup
    [Data_Logger_Board.kicad_pcb, MCU.kicad_sch, PWR.kicad_sch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]
2025-12-04 Layout for LoRa Radio
    [Data_Logger_Board.kicad_pcb]
2025-12-05 partial MCU layout
    [BAROMETER.kicad_sch, Data_Logger_Board.kicad_pcb, Data_Logger_Board.kicad_sch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]
2025-12-05 more progress on MCU layout
    [Data_Logger_Board.kicad_pcb, MAGNETOMETER.kicad_sch, MCU.kicad_sch]
2025-12-05 more MCU layout
    [Data_Logger_Board.kicad_pcb, GPS.kicad_sch]
2025-12-05 reorg board for pictures
    [Data_Logger_Board.kicad_pcb]
2025-12-05 fix footprint errors
    [BAROMETER.kicad_sch, Data_Logger_Board.kicad_pcb, IMU.kicad_sch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]
2025-12-06 add microSD
    [Data_Logger_Board.kicad_pcb, MCU.kicad_sch, microSD.kicad_sch]
2025-12-07 footprint + sd tweaks
    [BAROMETER.kicad_sch, Data_Logger_Board.kicad_pcb, Data_Logger_Board.kicad_sch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]
2026-01-06 update footprint
    [BAROMETER.kicad_sch, Data_Logger_Board.kicad_pcb, Data_Logger_Board.kicad_sch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]
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2026-01-10 Floor Planned PCB layout
    [Data_Logger_Board.kicad_pcb, MCU.kicad_sch]
2026-01-10 add WiFi 3D model
    [0479480001.step, Data_Logger_Board.kicad_pcb]
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2026-01-17 Layout
    Fixed via sizing, routed fanout from ESP
    [Data_Logger_Board.kicad_pcb, RF_LORA.kicad_sch]
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2026-01-23 update back plane fill settings
    [Data_Logger_Board.kicad_pcb]
2026-01-23 fix BMI footprint and resolve some errors
    [Data_Logger_Board.kicad_pcb]
2026-01-24 Updates to board routing
    Added SMA connector for radio, added additional SPI routing. Reworked some routing for other modules.
    [Data_Logger_Board.kicad_pcb, MCU.kicad_sch]
2026-01-25 layout
    fix rf, usb netclass, add timepulse, round dimensions to even number, re-route GPS, 22 ohm in usb line, buttons to front, reg to front, change solder jumper for conn
    [Data_Logger_Board.kicad_pcb, GPS.kicad_sch, MCU.kicad_sch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]
2026-01-28 round corners, place mounting holes
    [Data_Logger_Board.kicad_pcb]
2026-01-30 finish SPI routing +silkscreen tidy
    [Data_Logger_Board.kicad_pcb]
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2026-01-31 Corrected DRC Errors
    Added 220Ohm resistor to TCXO output.
    Fixed DRC Errors
    Added stitching vias
    [Data_Logger_Board.kicad_pcb, RF_LORA.kicad_sch]
2026-01-31 fix missing gnd
    [Data_Logger_Board.kicad_pcb]
2026-01-31 fix gps line
    [Data_Logger_Board.kicad_pcb]
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2026-02-01 update pcb from schem
    [Data_Logger_Board.kicad_pcb, MCU.kicad_sch]
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2026-02-03 fix battery sense + AIAA logo
    [Data_Logger_Board.kicad_pcb, MCU.kicad_sch]
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2026-02-04 add gnd vias below antenna
    [Data_Logger_Board.kicad_pcb, MCU.kicad_sch]
2026-02-04 Corrected RF Switch polarity
    [Data_Logger_Board.kicad_pcb, RF_LORA.kicad_sch]
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2026-02-05 remove units for extraction
    [BAROMETER.kicad_sch, Data_Logger_Board.kicad_pcb, IMU.kicad_sch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]
2026-02-05 fix netclass and rm bkp
    [RF_LORA.kicad_sch]
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2026-02-05 fix connections
    [Data_Logger_Board.kicad_pcb]
2026-02-06 fix silkscreen
    [Data_Logger_Board.kicad_pcb]
2026-02-06 fix merge
    [Data_Logger_Board.kicad_pcb]
2026-02-06 3v3 routing with fat traces
    [Data_Logger_Board.kicad_pcb]
2026-02-07 remove extra vias, tidy silkscreen warnings
    [Data_Logger_Board.kicad_pcb]
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2026-02-07 add more stitching vias
    [Data_Logger_Board.kicad_pcb]
2026-02-07 fix silk and re-align drill holes
    [Data_Logger_Board.kicad_pcb]
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2026-02-10 add tooling holes, rm mt hole symbol
    [Data_Logger_Board.kicad_pcb, MCU.kicad_sch]
2026-02-13 match trace widths to 4 layer
    [Data_Logger_Board.kicad_pcb]
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2026-03-21 Fix pin typo
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
